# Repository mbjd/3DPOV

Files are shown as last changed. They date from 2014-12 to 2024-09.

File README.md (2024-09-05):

# 3DPOV

This is the github repo for my 3D persistence of vision display. Here you
can find the arduino/teensy source code (`./code/`), eagle schematic and
board files (`./Eagle/`), and the python program I wrote to simplify the
creation of images containing simple shapes (`./image_creation/`).

### Videos

[one](https://www.youtube.com/watch?v=bCETWNgBxbI) [two](https://www.youtube.com/watch?v=-gFsKhf5J-I)

### Summary

This was my Matura project (the end of (the equivalent of) high school in
Switzerland), and I did most of the work in the second half of 2014. You
can find various more detailed reports below, but here's a quick summary:

The *very* basic idea is this: We have a 2D display
and rotate it quickly through the third dimension. By controlling each 
pixel in a precisely timed way, we can light up a set of points in 3D 
space, but only at specific times (when the corresponding pixel is
physically at the right spot). When this rotation is fast enough, 
[persistence of vision](https://en.wikipedia.org/wiki/Persistence_of_vision) 
will make it seem like an actual 3D image is continuously displayed. 

The display itself consists of 10 LED rows mounted in a double-helix
arrangement. Each of them contains 16 RGB LEDs driven by three shift
registers, for a total of 480 LEDs or 160 Pixels.

The shift registers are controlled by a Teensy 3.1 microcontroller board
using an SPI bus (All 30 shift registers are daisy chained together). The
controller is mounted on a wooden disc below the ten LED boards.

All of this is mounted on a 4mm steel shaft, supplied with 3.3V DC using
two copper slip rings, and spun up to 60 Hz by a brushed DC motor. A hall
sensor and a magnet enable the controller to measure the rotational speed
and to adjust its timing, so that the image always stays still despite the
speed not being quite constant. The image is updated 100 times per
revolution, or 6000 times a second.

Currently there's no way to supply images at runtime, the display has to be
stopped so that a new program can be uploaded using the Teensy's USB port.

### Various versions of the paper

[Original in German](https://drive.google.com/file/d/0B2iq6C3wqe05aEx5dVFoNF9xR28/view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)

[English long version, not quite finished](https://github.com/mbjd/english-paper/blob/master/paper.pdf)

[English short version](https://github.com/mbjd/english-paper/blob/master/paper-short.pdf)

[Other english stuff](https://github.com/mbjd/english-paper)

### Press etc

[Hackaday article](http://hackaday.com/2016/11/16/spinning-3d-pov-display-as-a-high-school-term-project/)

[ETHZ D-ITET in German](https://www.ee.ethz.ch/de/news-und-veranstaltungen/d-itet-news-channel/2016/09/d-itet-student-gewinnt-forschungs-preis-.html) or [English](https://www.ee.ethz.ch/news-and-events/d-itet-news-channel/2016/09/d-itet-student-wins-research-award.html)

[Swiss Youth in Science article](http://web.archive.org/web/20161117130814/http://sjf.ch/eucys-2016-eth-student-gewinnt-forschungs-preis-am-ersten-studientag/)

[EUCYS 2016 link](http://eucys2016.eu/development-of-a-3d-display/)

### Links to discussion

[one](http://www.reddit.com/r/electronics/comments/2m6apx/finally_my_led_board_works_had_to_make_a_little/) [two](http://www.reddit.com/r/electronics/comments/2nrek4/almost_working_3d_pov_display/) [three](http://www.reddit.com/r/electronics/comments/2q9sg6/my_3d_pov_in_action_as_promised/)

### Photos

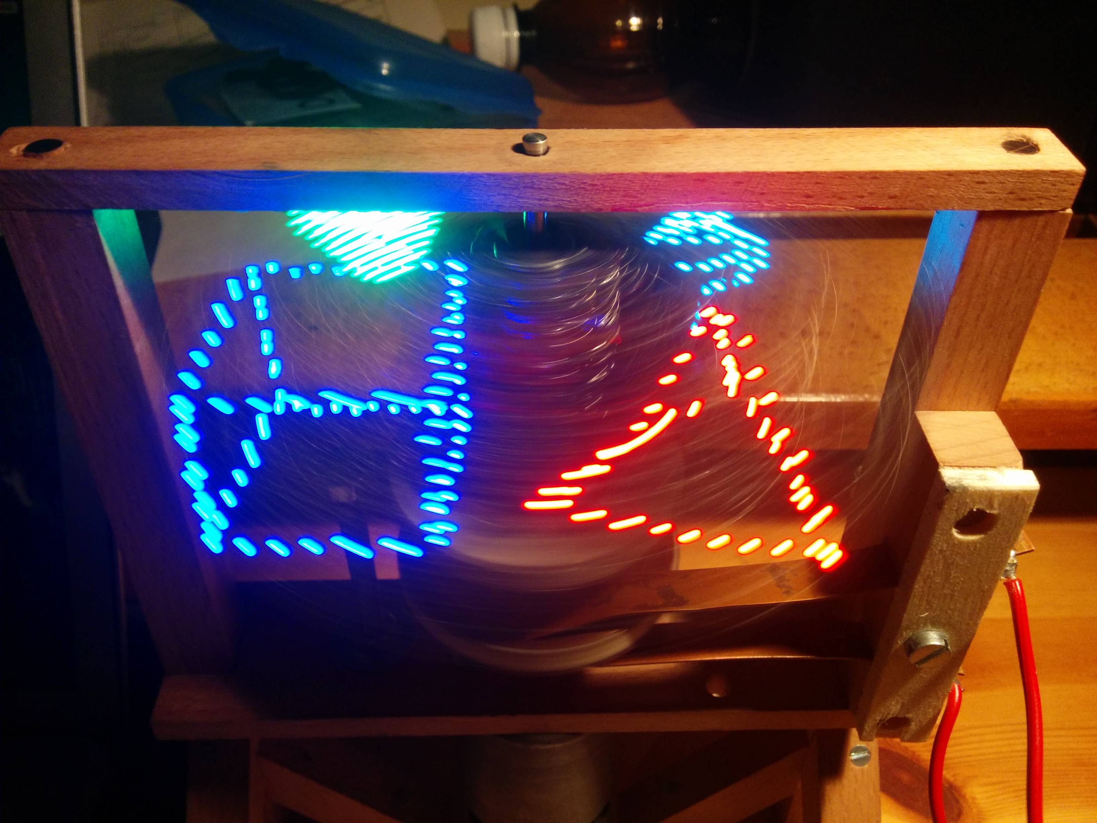
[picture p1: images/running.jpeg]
Photo of it in action


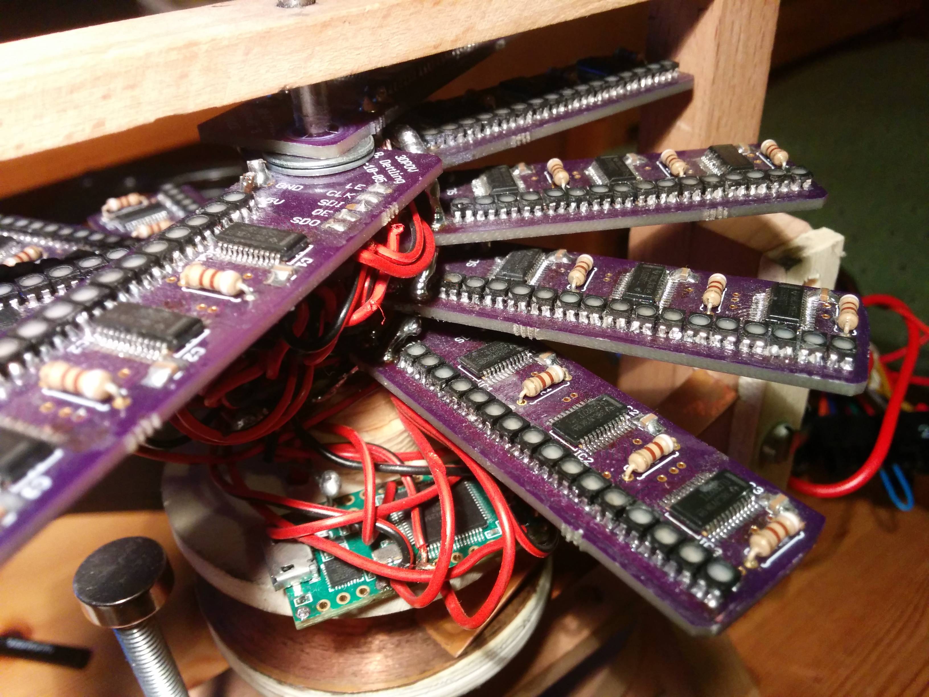
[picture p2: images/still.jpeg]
Photo of it standing still


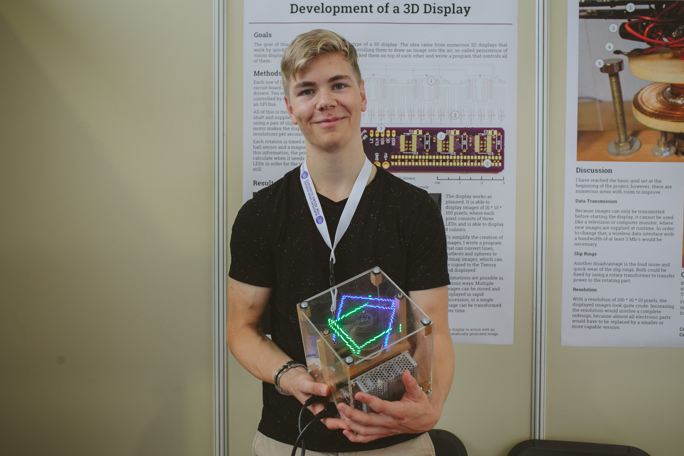
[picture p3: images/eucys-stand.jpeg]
Me at EUCYS 2016 being super happy


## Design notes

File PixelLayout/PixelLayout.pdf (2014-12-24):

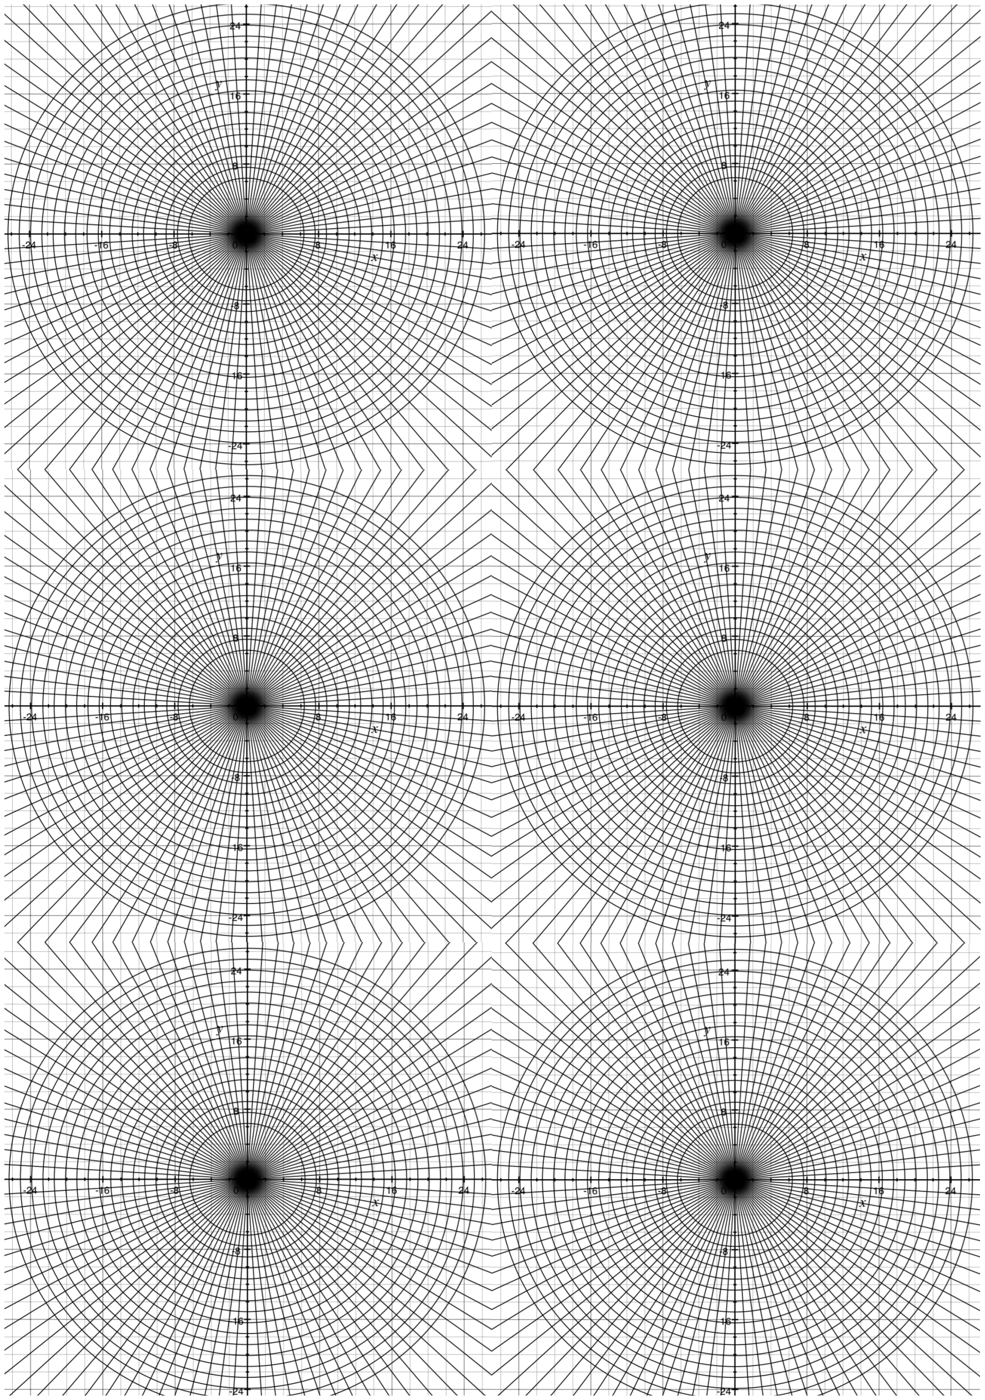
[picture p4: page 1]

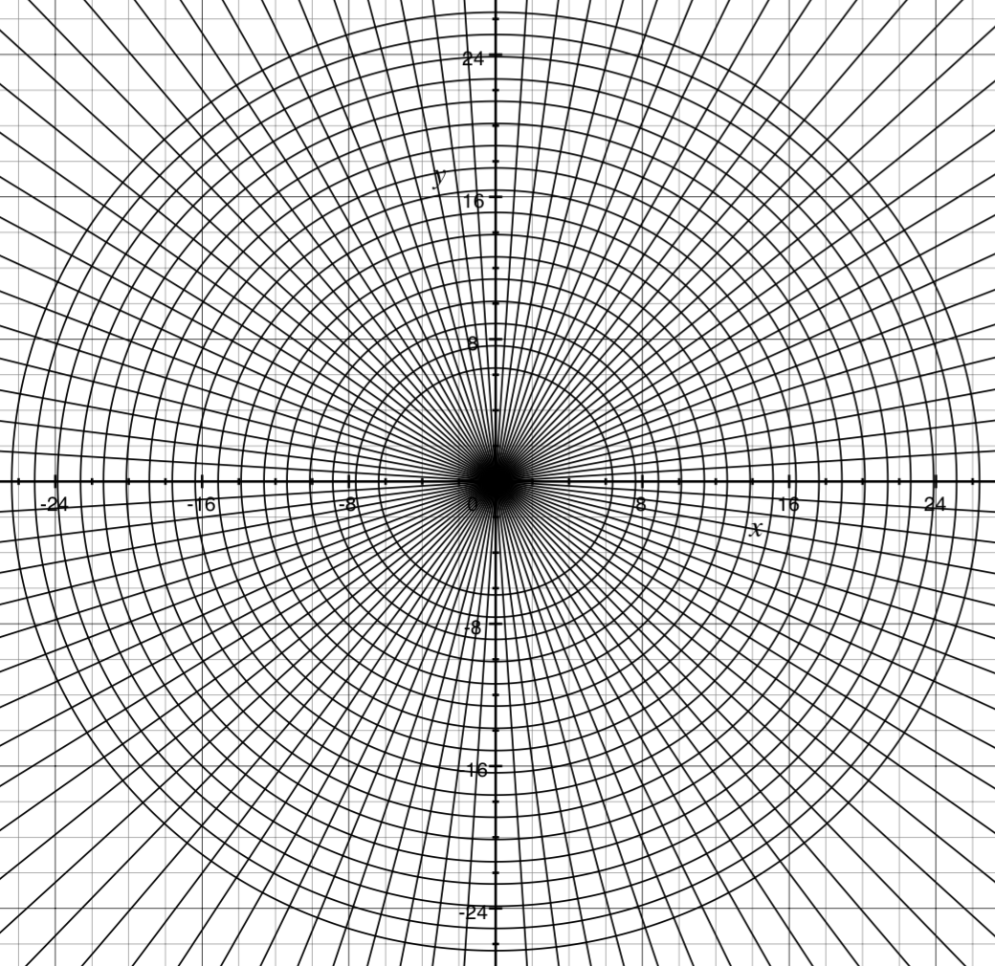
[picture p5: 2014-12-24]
PixelLayout/PixelLayout.png

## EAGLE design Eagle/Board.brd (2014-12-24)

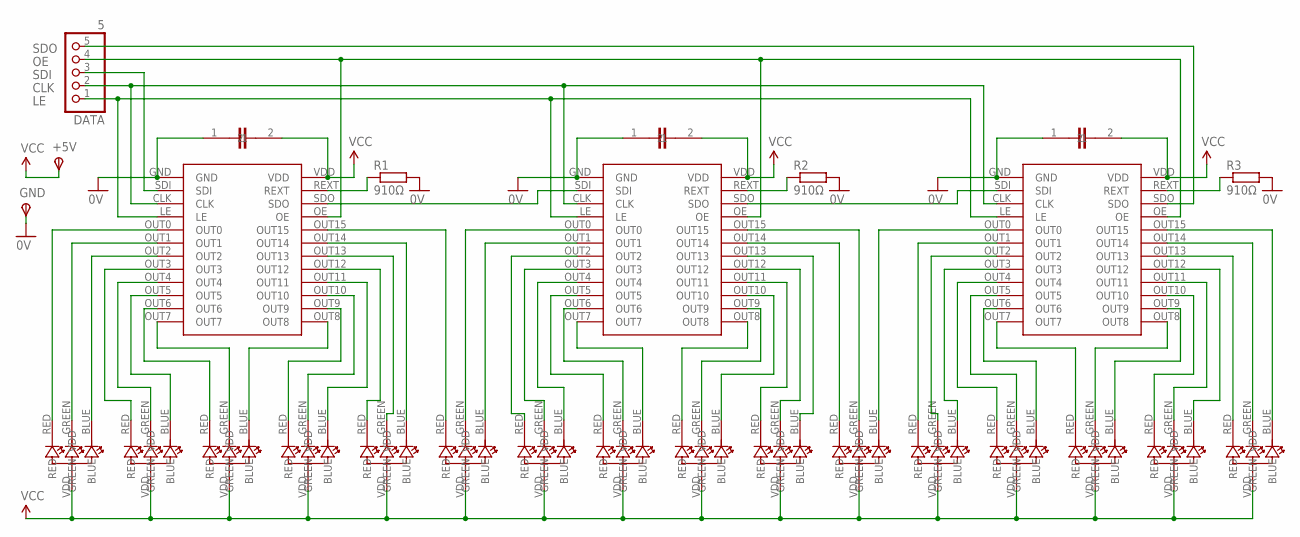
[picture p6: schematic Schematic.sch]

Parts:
+5V: TPSPAD1-20; P1-20
CAP1, CAP2, CAP3: 1µF; CAP
DATA: 5; 1X05
GND: TPSPAD1-20; P1-20
IC1, IC2, IC3: TLC5927; DBQ
R1, R2, R3: 910Ω; 0207/7
U$1, U$2, U$4, U$5, U$6, U$7, U$10, U$11, U$12, U$13, U$14, U$15, U$16, U$17, U$18, U$19: SMDLED

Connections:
0V: CAP1.1, CAP2.1, CAP3.1, GND.TP, IC1.GND, IC2.GND, IC3.GND, R1.2, R2.2, R3.2
CLK: DATA.2, IC1.CLK, IC2.CLK, IC3.CLK
LE: DATA.1, IC1.LE, IC2.LE, IC3.LE
unnamed: IC1.OUT0, U$4.RED
unnamed: IC1.OUT1, U$4.GREEN
unnamed: IC1.OUT2, U$4.BLUE
unnamed: IC1.OUT3, U$5.RED
unnamed: IC1.OUT4, U$5.GREEN
unnamed: IC1.OUT5, U$5.BLUE
unnamed: IC1.OUT7, U$6.GREEN
unnamed: IC1.OUT6, U$6.RED
unnamed: IC1.OUT8, U$6.BLUE
unnamed: IC1.OUT9, U$7.RED
unnamed: IC1.OUT10, U$7.GREEN
unnamed: IC1.OUT11, U$7.BLUE
unnamed: IC1.OUT12, U$2.RED
unnamed: IC1.OUT13, U$2.GREEN
unnamed: IC1.OUT14, U$2.BLUE
unnamed: IC1.OUT15, U$1.RED
unnamed: IC2.OUT0, U$1.GREEN
unnamed: IC2.OUT1, U$1.BLUE
unnamed: IC2.OUT2, U$10.RED
unnamed: IC2.OUT3, U$10.GREEN
unnamed: IC2.OUT4, U$10.BLUE
unnamed: IC2.OUT7, U$11.BLUE
unnamed: IC2.OUT6, U$11.GREEN
unnamed: IC2.OUT5, U$11.RED
unnamed: IC2.OUT11, U$13.RED
unnamed: IC2.OUT12, U$13.GREEN
unnamed: IC2.OUT13, U$13.BLUE
unnamed: IC2.OUT14, U$14.RED
unnamed: IC2.OUT15, U$14.GREEN
unnamed: IC3.OUT0, U$14.BLUE
unnamed: IC3.OUT1, U$15.RED
unnamed: IC3.OUT2, U$15.GREEN
unnamed: IC3.OUT3, U$15.BLUE
unnamed: IC3.OUT4, U$16.RED
unnamed: IC3.OUT5, U$16.GREEN
unnamed: IC3.OUT7, U$17.RED
unnamed: IC3.OUT6, U$16.BLUE
unnamed: IC3.OUT8, U$17.GREEN
unnamed: IC3.OUT9, U$17.BLUE
unnamed: IC3.OUT10, U$18.RED
unnamed: IC3.OUT11, U$18.GREEN
unnamed: IC3.OUT12, U$18.BLUE
unnamed: IC3.OUT13, U$19.RED
unnamed: IC3.OUT14, U$19.GREEN
unnamed: IC3.OUT15, U$19.BLUE
unnamed: IC3.REXT, R3.1
unnamed: IC1.SDO, IC2.SDI
unnamed: IC2.SDO, IC3.SDI
unnamed: IC2.REXT, R2.1
unnamed: IC1.REXT, R1.1
unnamed: IC2.OUT8, U$12.RED
unnamed: IC2.OUT9, U$12.GREEN
unnamed: IC2.OUT10, U$12.BLUE
OE: DATA.4, IC1.OE, IC2.OE, IC3.OE
SDI: DATA.3, IC1.SDI
SDO: DATA.5, IC3.SDO
VCC: +5V.TP, CAP1.2, CAP2.2, CAP3.2, IC1.VDD, IC2.VDD, IC3.VDD, U$1.VDD, U$2.VDD, U$4.VDD, U$5.VDD, U$6.VDD, U$7.VDD, U$10.VDD, U$11.VDD, U$12.VDD, U$13.VDD, U$14.VDD, U$15.VDD, U$16.VDD, U$17.VDD, U$18.VDD, U$19.VDD

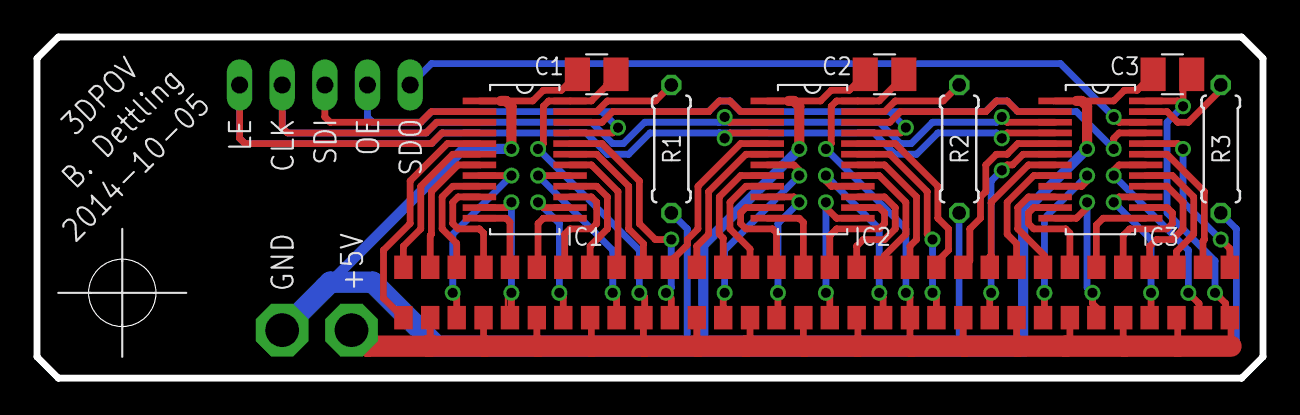
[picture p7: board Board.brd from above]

Board: 2 copper layers, 73.0 x 20.3 mm, 28 parts (0 on the bottom side), 60 nets.

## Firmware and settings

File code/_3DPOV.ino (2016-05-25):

#include <SPI.h>

const byte image[100][10][16] = {
	// 00
	{
		{0b00000000, 0b00000000, 0b00000000, 0b00000000, 0b00000000, 0b00000000},
		{0b00000000, 0b00000000, 0b00000000, 0b00000000, 0b00000000, 0b00000000},
		{0b00000000, 0b00000000, 0b00000000, 0b00000000, 0b00000000, 0b00000000},
		{0b00000000, 0b00000000, 0b00000000, 0b00000000, 0b00000000, 0b00000000},
		{0b00000000, 0b00000000, 0b00000000, 0b00000000, 0b00000000, 0b00000000},
		{0b00000000, 0b00000000, 0b00000000, 0b00000000, 0b00000000, 0b00000000},
		{0b00000000, 0b00000000, 0b00000000, 0b00000000, 0b00000000, 0b00000000},
		{0b00000000, 0b00000000, 0b00000000, 0b00000000, 0b00000000, 0b00000000},
		{0b00000000, 0b00000000, 0b00000000, 0b00000000, 0b00000000, 0b00000000},
		{0b00000000, 0b00000000, 0b00000000, 0b00000000, 0b00000000, 0b00000000}
	},

	// 01
	{
		{0b00000000, 0b00000000, 0b00000000, 0b00000000, 0b00000000, 0b00000000},
		{0b00000000, 0b00000000, 0b00000000, 0b00000000, 0b00000000, 0b00000000},
		{0b00000000, 0b00000000, 0b00000000, 0b00000000, 0b00000000, 0b00000000},
		{0b00000000, 0b00000000, 0b00000000, 0b00000000, 0b00000000, 0b00000000},
		{0b00000000, 0b00000000, 0b00000000, 0b00000000, 0b00000000, 0b00000000},
		{0b00000000, 0b00000000, 0b00000000, 0b00000000, 0b00000000, 0b00000000},
		{0b00000000, 0b00000000, 0b00000000, 0b00000000, 0b00000000, 0b00000000},
		{0b00000000, 0b00000000, 0b00000000, 0b00000000, 0b00000000, 0b00000000},
		{0b00000000, 0b00000000, 0b00000000, 0b00000000, 0b00000000, 0b00000000},
		{0b00000000, 0b00000000, 0b00000000, 0b00000000, 0b00000000, 0b00000000}
	},

	// 02
	{
		{0b00000000, 0b00000000, 0b00000000, 0b00000000, 0b00000000, 0b00000000},
		{0b00000000, 0b00000000, 0b00000000, 0b00000000, 0b00000000, 0b00000000},
		{0b00000000, 0b00000000, 0b00000000, 0b00000000, 0b00000000, 0b00000000},
		{0b00000000, 0b00000000, 0b00000000, 0b00000000, 0b00000000, 0b00000000},
		{0b00000000, 0b00000000, 0b00000000, 0b00000000, 0b00000000, 0b00000000},
		{0b00000000, 0b00000000, 0b00000000, 0b00000000, 0b00000000, 0b00000000},
		{0b00000000, 0b00000000, 0b00000000, 0b00000000, 0b00000000, 0b00000000},
		{0b00000000, 0b00000000, 0b00000000, 0b00000000, 0b00000000, 0b00000000},
		{0b00000000, 0b00000000, 0b00000000, 0b00000000, 0b00000000, 0b00000000},
		{0b00000000, 0b00000000, 0b00000000, 0b00000000, 0b00000000, 0b00000000}
	},

	// 03
	{
		{0b00000000, 0b00000000, 0b00000000, 0b00000000, 0b00000000, 0b00000000},
		{0b00000000, 0b00000000, 0b00000000, 0b00000000, 0b00000000, 0b00000000},
		{0b00000000, 0b00000000, 0b00000000, 0b00000000, 0b00000000, 0b00000000},
		{0b00000000, 0b00000000, 0b00000000, 0b00000000, 0b00000000, 0b00000000},
		{0b00000000, 0b00000000, 0b00000000, 0b00000000, 0b00000000, 0b00000000},
		{0b00000000, 0b00000000, 0b00000000, 0b00000000, 0b00000000, 0b00000000},
		{0b00000000, 0b00000000, 0b00000000, 0b00000000, 0b00000000, 0b00000000},
		{0b00000000, 0b00000000, 0b00000000, 0b00000000, 0b00000000, 0b00000000},
		{0b00000000, 0b00000000, 0b00000000, 0b00000000, 0b00000000, 0b00000000},
		{0b00000000, 0b00000000, 0b00000000, 0b00000000, 0b00000000, 0b00000000}
	},

	// 04
	{
		{0b00000000, 0b00000000, 0b00000000, 0b00000000, 0b00000000, 0b00000000},
		{0b00000000, 0b00000000, 0b00000000, 0b00000000, 0b00000000, 0b00000000},
		{0b00000000, 0b00000000, 0b00000000, 0b00000000, 0b00000000, 0b00000000},
		{0b00000000, 0b00000000, 0b00000000, 0b00000000, 0b00000000, 0b00000000},
		{0b00000000, 0b00000000, 0b00000000, 0b00000000, 0b00000000, 0b00000000},
		{0b00000000, 0b00000000, 0b00000000, 0b00000000, 0b00000000, 0b00000000},
		{0b00000000, 0b00000000, 0b00000000, 0b00000000, 0b00000000, 0b00000000},
		{0b00000000, 0b00000000, 0b00000000, 0b00000000, 0b00000000, 0b00000000},
		{0b00000000, 0b00000000, 0b00000000, 0b00000000, 0b00000000, 0b00000000},
		{0b00000000, 0b00000000, 0b00000000, 0b00000000, 0b00000000, 0b00000000}
	},

	// 05
	{
		{0b00000000, 0b00000000, 0b00000000, 0b00000000, 0b00000000, 0b00000000},
		{0b00000000, 0b00000000, 0b00000000, 0b00000000, 0b00000000, 0b00000000},
		{0b00000000, 0b00000000, 0b00000000, 0b00000000, 0b00000000, 0b00000000},
		{0b00000000, 0b00000000, 0b00000000, 0b00000000, 0b00000000, 0b00000000},
		{0b00000000, 0b00000000, 0b00000000, 0b00000000, 0b00000000, 0b00000000},
		{0b00000000, 0b00000000, 0b00000000, 0b00000000, 0b00000000, 0b00000000},
		{0b00000000, 0b00000000, 0b00000000, 0b00000000, 0b00000000, 0b00000000},
		{0b00000000, 0b00000000, 0b00000000, 0b00000000, 0b00000000, 0b00000000},
		{0b00000000, 0b00000000, 0b00000000, 0b00000000, 0b00000000, 0b00000000},
		{0b00000000, 0b00000000, 0b00000000, 0b00000000, 0b00000000, 0b00000000}
	},

	// 06
	{
		{0b00000000, 0b00000000, 0b00000000, 0b00000000, 0b00000000, 0b00000000},
		{0b00000000, 0b00000000, 0b00000000, 0b00000000, 0b00000000, 0b00000000},
		{0b00000000, 0b00000000, 0b00000000, 0b00000000, 0b00000000, 0b00000000},
		{0b00000000, 0b00000000, 0b00000000, 0b00000000, 0b00000000, 0b00000000},
		{0b00000000, 0b00000000, 0b00000000, 0b00000000, 0b00000000, 0b00000000},
		{0b00000000, 0b00000000, 0b00000000, 0b00000000, 0b00000000, 0b00000000},
		{0b00000000, 0b00000000, 0b00000000, 0b00000000, 0b00000000, 0b00000000},
		{0b00000000, 0b00000000, 0b00000000, 0b00000000, 0b00000000, 0b00000000},
		{0b00000000, 0b00000000, 0b00000000, 0b00000000, 0b00000000, 0b00000000},
		{0b00000000, 0b00000000, 0b00000000, 0b00000000, 0b00000000, 0b00000000}
	},

	// 07
	{
		{0b00000000, 0b00000000, 0b00000000, 0b00000000, 0b00000000, 0b00000000},
		{0b00000000, 0b00000000, 0b00000000, 0b00000000, 0b00000000, 0b00000000},
		{0b00000000, 0b00000000, 0b00000000, 0b00000000, 0b00000000, 0b00000000},
		{0b00000000, 0b00000000, 0b00000000, 0b00000000, 0b00000000, 0b00000000},
		{0b00000000, 0b00000000, 0b00000000, 0b00000000, 0b00000000, 0b00000000},
		{0b00000000, 0b00000000, 0b00000000, 0b00000000, 0b00000000, 0b00000000},
		{0b00000000, 0b00000000, 0b00000000, 0b00000000, 0b00000000, 0b00000000},
		{0b00000000, 0b00000000, 0b00000000, 0b00000000, 0b00000000, 0b00000000},
		{0b00000000, 0b00000000, 0b00000000, 0b00000000, 0b00000000, 0b00000000},
		{0b00000000, 0b00000000, 0b00000000, 0b00000000, 0b00000000, 0b00000000}
	},

	// 08
	{
		{0b00000000, 0b00000000, 0b00000000, 0b00000000, 0b00000000, 0b00000000},
		{0b00000000, 0b00000000, 0b00000000, 0b00000000, 0b00000000, 0b00000000},
		{0b00000000, 0b00000000, 0b00000000, 0b00000000, 0b00000000, 0b00000000},
		{0b00000000, 0b00000000, 0b00000000, 0b00000000, 0b00000000, 0b00000000},
		{0b00000000, 0b00000000, 0b00000000, 0b00000000, 0b00000000, 0b00000000},
		{0b00000000, 0b00000000, 0b00000000, 0b00000000, 0b00000000, 0b00000000},
		{0b00000000, 0b00000000, 0b00000000, 0b00000000, 0b00000000, 0b00000000},
		{0b00000000, 0b00000000, 0b00000000, 0b00000000, 0b00000000, 0b00000000},
		{0b00000000, 0b00000000, 0b00000000, 0b00000000, 0b00000000, 0b00000000},
		{0b00000000, 0b00000000, 0b00000000, 0b00000000, 0b00000000, 0b00000000}
	},

	// 09
	{
		{0b00000000, 0b00000000, 0b00000000, 0b00000000, 0b00000000, 0b00000000},
		{0b00000000, 0b00000000, 0b00000000, 0b00000000, 0b00000000, 0b00000000},
		{0b00000000, 0b00000000, 0b00000000, 0b00000000, 0b00000000, 0b00000000},
		{0b00000000, 0b00000000, 0b00000000, 0b00000000, 0b00000000, 0b00000000},
		{0b00000000, 0b00000000, 0b00000000, 0b00000000, 0b00000000, 0b00000000},
		{0b00000000, 0b00000000, 0b00000000, 0b00000000, 0b00000000, 0b00000000},
		{0b00000000, 0b00000000, 0b00000000, 0b00000000, 0b00000000, 0b00000000},
		{0b00000000, 0b00000000, 0b00000000, 0b00000000, 0b00000000, 0b00000000},
		{0b00000000, 0b00000000, 0b00000000, 0b00000000, 0b00000000, 0b00000000},
		{0b00000000, 0b00000000, 0b00000000, 0b00000000, 0b00000000, 0b00000000}
	},

	// 10
	{
		{0b00000000, 0b00000000, 0b00000000, 0b00000000, 0b00000000, 0b00000000},
		{0b00000000, 0b00000000, 0b00000000, 0b00000000, 0b00000000, 0b00000000},
		{0b00000000, 0b00000000, 0b00000000, 0b00000000, 0b00000000, 0b00000000},
		{0b00000000, 0b00000000, 0b00000000, 0b00000000, 0b00000000, 0b00000000},
		{0b00000000, 0b00000000, 0b00000000, 0b00000000, 0b00000000, 0b00000000},
		{0b00000000, 0b00000000, 0b00000000, 0b00000000, 0b00000000, 0b00000000},
		{0b00000000, 0b00000000, 0b00000000, 0b00000000, 0b00000000, 0b00000000},
		{0b00000000, 0b00000000, 0b00000000, 0b00000000, 0b00000000, 0b00000000},
		{0b00000000, 0b00000000, 0b00000000, 0b00000000, 0b00000000, 0b00000000},
		{0b00000000, 0b00000000, 0b00000000, 0b00000000, 0b00000000, 0b00000000}
	},

	// 11
	{
		{0b00000000, 0b00000000, 0b00000000, 0b00000000, 0b00000000, 0b00000000},
		{0b00000000, 0b00000000, 0b00000000, 0b00000000, 0b00000000, 0b00000000},
		{0b00000000, 0b00000000, 0b00000000, 0b00000000, 0b00000000, 0b00000000},
		{0b00000000, 0b00000000, 0b00000000, 0b00000000, 0b00000000, 0b00000000},
		{0b00000000, 0b00000000, 0b00000000, 0b00000000, 0b00000000, 0b00000000},
		{0b00000000, 0b00000000, 0b00000000, 0b00000000, 0b00000000, 0b00000000},
		{0b00000000, 0b00000000, 0b00000000, 0b00000000, 0b00000000, 0b00000000},
		{0b00000000, 0b00000000, 0b00000000, 0b00000000, 0b00000000, 0b00000000},
		{0b00000000, 0b00000000, 0b00000000, 0b00000000, 0b00000000, 0b00000000},
		{0b00000000, 0b00000000, 0b00000000, 0b00000000, 0b00000000, 0b00000000}
	},

	// 12
	{
		{0b00000000, 0b00000000, 0b00000000, 0b00000000, 0b00000000, 0b00000000},
		{0b00000000, 0b00000000, 0b00000000, 0b00000000, 0b00000000, 0b00000000},
		{0b00000000, 0b00000000, 0b00000000, 0b00000000, 0b00000000, 0b00000000},
		{0b00000000, 0b00000000, 0b00000000, 0b00000000, 0b00000000, 0b00000000},
		{0b00000000, 0b00000000, 0b00000000, 0b00000000, 0b00000000, 0b00000000},
		{0b00000000, 0b00000000, 0b00000000, 0b00000000, 0b00000000, 0b00000000},
		{0b00000000, 0b00000000, 0b00000000, 0b00000000, 0b00000000, 0b00000000},
		{0b00000000, 0b00000000, 0b00000000, 0b00000000, 0b00000000, 0b00000000},
		{0b00000000, 0b00000000, 0b00000000, 0b00000000, 0b00000000, 0b00000000},
		{0b00000000, 0b00000000, 0b00000000, 0b00000000, 0b00000000, 0b00000000}
	},

	// 13
	{
		{0b00000000, 0b00000000, 0b00000000, 0b00000000, 0b00000000, 0b00000000},
		{0b00000000, 0b00000000, 0b00000000, 0b00000000, 0b00000000, 0b00000000},
		{0b00000000, 0b00000000, 0b00000000, 0b00000000, 0b00000000, 0b00000000},
		{0b00000000, 0b00000000, 0b00000000, 0b00000000, 0b00000000, 0b00000000},
		{0b00000000, 0b00000000, 0b00000000, 0b00000000, 0b00000000, 0b00000000},
		{0b00000000, 0b00000000, 0b00000000, 0b00000000, 0b00000000, 0b00000000},
		{0b00000000, 0b00000000, 0b00000000, 0b00000000, 0b00000000, 0b00000000},
		{0b00000000, 0b00000000, 0b00000000, 0b00000000, 0b00000000, 0b00000000},
		{0b00000000, 0b00000000, 0b00000000, 0b00000000, 0b00000000, 0b00000000},
		{0b00000000, 0b00000000, 0b00000000, 0b00000000, 0b00000000, 0b00000000}
	},

	// 14
	{
		{0b00000000, 0b00000000, 0b00000000, 0b00000000, 0b00000000, 0b00000000},
		{0b00000000, 0b00000000, 0b00000000, 0b00000000, 0b00000000, 0b00000000},
		{0b00000000, 0b00000000, 0b00000000, 0b00000000, 0b00000000, 0b00000000},
		{0b00000000, 0b00000000, 0b00000000, 0b00000000, 0b00000000, 0b00000000},
		{0b00000000, 0b00000000, 0b00000000, 0b00000000, 0b00000000, 0b00000000},
		{0b00000000, 0b00000000, 0b00000000, 0b00000000, 0b00000000, 0b00000000},
		{0b00000000, 0b00000000, 0b00000000, 0b00000000, 0b00000000, 0b00000000},
		{0b00000000, 0b00000000, 0b00000000, 0b00000000, 0b00000000, 0b00000000},
		{0b00000000, 0b00000000, 0b00000000, 0b00000000, 0b00000000, 0b00000000},
		{0b00000000, 0b00000000, 0b00000000, 0b00000000, 0b00000000, 0b00000000}
	},

	// 15
	{
		{0b00000000, 0b00000000, 0b00000000, 0b00000000, 0b00000000, 0b00000000},
		{0b00000000, 0b00000000, 0b00000000, 0b00000000, 0b00000000, 0b00000000},
		{0b00000000, 0b00000000, 0b00000000, 0b00000000, 0b00000000, 0b00000000},
		{0b00000000, 0b00000000, 0b00000000, 0b00000000, 0b00000000, 0b00000000},
		{0b00000000, 0b00000000, 0b00000000, 0b00000000, 0b00000000, 0b00000000},
		{0b00000000, 0b00000000, 0b00000000, 0b00000000, 0b00000000, 0b00000000},
		{0b00000000, 0b00000000, 0b00000000, 0b00000000, 0b00000000, 0b00000000},
		{0b00000000, 0b00000000, 0b00000000, 0b00000000, 0b00000000, 0b00000000},
		{0b00000000, 0b00000000, 0b00000000, 0b00000000, 0b00000000, 0b00000000},
		{0b00000000, 0b00000000, 0b00000000, 0b00000000, 0b00000000, 0b00000000}
	},

	// 16
	{
		{0b00000000, 0b00000000, 0b00000000, 0b00000000, 0b00000000, 0b00000000},
		{0b00000000, 0b00000000, 0b00000000, 0b00000000, 0b00000000, 0b00000000},
		{0b00000000, 0b00000000, 0b00000000, 0b00000000, 0b00000000, 0b00000000},
		{0b00000000, 0b00000000, 0b00000000, 0b00000000, 0b00000000, 0b00000000},
		{0b00000000, 0b00000000, 0b00000000, 0b00000000, 0b00000000, 0b00000000},
		{0b00000000, 0b00000000, 0b00000000, 0b00000000, 0b00000000, 0b00000000},
		{0b00000000, 0b00000000, 0b00000000, 0b00000000, 0b00000000, 0b00000000},
		{0b00000000, 0b00000000, 0b00000000, 0b00000000, 0b00000000, 0b00000000},
		{0b00000000, 0b00000000, 0b00000000, 0b00000000, 0b00000000, 0b00000000},
		{0b00000000, 0b00000000, 0b00000000, 0b00000000, 0b00000000, 0b00000000}
	},

	// 17
	{
		{0b00000000, 0b00000000, 0b00000000, 0b00000000, 0b00000000, 0b00000000},
		{0b00000000, 0b00000000, 0b00000000, 0b00000000, 0b00000000, 0b00000000},
		{0b00000000, 0b00000000, 0b00000000, 0b00000000, 0b00000000, 0b00000000},
		{0b00000000, 0b00000000, 0b00000000, 0b00000000, 0b00000000, 0b00000000},
		{0b00000000, 0b00000000, 0b00000000, 0b00000000, 0b00000000, 0b00000000},
		{0b00000000, 0b00000000, 0b00000000, 0b00000000, 0b00000000, 0b00000000},
		{0b00000000, 0b00000000, 0b00000000, 0b00000000, 0b00000000, 0b00000000},
		{0b00000000, 0b00000000, 0b00000000, 0b00000000, 0b00000000, 0b00000000},
		{0b00000000, 0b00000000, 0b00000000, 0b00000000, 0b00000000, 0b00000000},
		{0b00000000, 0b00000000, 0b00000000, 0b00000000, 0b00000000, 0b00000000}
	},

	// 18
	{
		{0b00000000, 0b00000000, 0b00000000, 0b00000000, 0b00000000, 0b00000000},
		{0b00000000, 0b00000000, 0b00000000, 0b00000000, 0b00000000, 0b00000000},
		{0b00000000, 0b00000000, 0b00000000, 0b00000000, 0b00000000, 0b00000000},
		{0b00000000, 0b00000000, 0b00000000, 0b00000000, 0b00000000, 0b00000000},
		{0b00000000, 0b00000000, 0b00000000, 0b00000000, 0b00000000, 0b00000000},
		{0b00000000, 0b00000000, 0b00000000, 0b00000000, 0b00000000, 0b00000000},
		{0b00000000, 0b00000000, 0b00000000, 0b00000000, 0b00000000, 0b00000000},
		{0b00000000, 0b00000000, 0b00000000, 0b00000000, 0b00000000, 0b00000000},
		{0b00000000, 0b00000000, 0b00000000, 0b00000000, 0b00000000, 0b00000000},
		{0b00000000, 0b00000000, 0b00000000, 0b00000000, 0b00000000, 0b00000000}
	},

	// 19
	{
		{0b00000000, 0b00000000, 0b00000000, 0b00000000, 0b00000000, 0b00000000},
		{0b00000000, 0b00000000, 0b00000000, 0b00000000, 0b00000000, 0b00000000},
		{0b00000000, 0b00000000, 0b00000000, 0b00000000, 0b00000000, 0b00000000},
		{0b00000000, 0b00000000, 0b00000000, 0b00000000, 0b00000000, 0b00000000},
		{0b00000000, 0b00000000, 0b00000000, 0b00000000, 0b00000000, 0b00000000},
		{0b00000000, 0b00000000, 0b00000000, 0b00000000, 0b00000000, 0b00000000},
		{0b00000000, 0b00000000, 0b00000000, 0b00000000, 0b00000000, 0b00000000},
		{0b00000000, 0b00000000, 0b00000000, 0b00000000, 0b00000000, 0b00000000},
		{0b00000000, 0b00000000, 0b00000000, 0b00000000, 0b00000000, 0b00000000},
		{0b00000000, 0b00000000, 0b00000000, 0b00000000, 0b00000000, 0b00000000}
	},

	// 20
	{
		{0b00000000, 0b00000000, 0b00000000, 0b00000000, 0b00000000, 0b00000000},
		{0b00000000, 0b00000000, 0b00000000, 0b00000000, 0b00000000, 0b00000000},
		{0b00000000, 0b00000000, 0b00000000, 0b00000000, 0b00000000, 0b00000000},
		{0b00000000, 0b00000000, 0b00000000, 0b00000000, 0b00000000, 0b00000000},
		{0b00000000, 0b00000000, 0b00000000, 0b00000000, 0b00000000, 0b00000000},
		{0b00000000, 0b00000000, 0b00000000, 0b00000000, 0b00000000, 0b00000000},
		{0b00000000, 0b00000000, 0b00000000, 0b00000000, 0b00000000, 0b00000000},
		{0b00000000, 0b00000000, 0b00000000, 0b00000000, 0b00000000, 0b00000000},
		{0b00000000, 0b00000000, 0b00000000, 0b00000000, 0b00000000, 0b00000000},
		{0b00000000, 0b00000000, 0b00000000, 0b00000000, 0b00000000, 0b00000000}
	},

	// 21
	{
		{0b00000000, 0b00000000, 0b00000000, 0b00000000, 0b00000000, 0b00000000},
		{0b00000000, 0b00000000, 0b00000000, 0b00000000, 0b00000000, 0b00000000},
		{0b00000000, 0b00000000, 0b00000000, 0b00000000, 0b00000000, 0b00000000},
		{0b00000000, 0b00000000, 0b00000000, 0b00000000, 0b00000000, 0b00000000},
		{0b00000000, 0b00000000, 0b00000000, 0b00000000, 0b00000000, 0b00000000},
		{0b00000000, 0b00000000, 0b00000000, 0b00000000, 0b00000000, 0b00000000},
		{0b00000000, 0b00000000, 0b00000000, 0b00000000, 0b00000000, 0b00000000},
		{0b00000000, 0b00000000, 0b00000000, 0b00000000, 0b00000000, 0b00000000},
		{0b00000000, 0b00000000, 0b00000000, 0b00000000, 0b00000000, 0b00000000},
		{0b00000000, 0b00000000, 0b00000000, 0b00000000, 0b00000000, 0b00000000}
	},

	// 22
	{
		{0b00000000, 0b00000000, 0b00000000, 0b00000000, 0b00000000, 0b00000000},
		{0b00000000, 0b00000000, 0b00000000, 0b00000000, 0b00000000, 0b00000000},
		{0b00000000, 0b00000000, 0b00000000, 0b00000000, 0b00000000, 0b00000000},
		{0b00000000, 0b00000000, 0b00000000, 0b00000000, 0b00000000, 0b00000000},
		{0b00000000, 0b00000000, 0b00000000, 0b00000000, 0b00000000, 0b00000000},
		{0b00000000, 0b00000000, 0b00000000, 0b00000000, 0b00000000, 0b00000000},
		{0b00000000, 0b00000000, 0b00000000, 0b00000000, 0b00000000, 0b00000000},
		{0b00000000, 0b00000000, 0b00000000, 0b00000000, 0b00000000, 0b00000000},
		{0b00000000, 0b00000000, 0b00000000, 0b00000000, 0b00000000, 0b00000000},
		{0b00000000, 0b00000000, 0b00000000, 0b00000000, 0b00000000, 0b00000000}
	},

	// 23
	{
		{0b00000000, 0b00000000, 0b00000000, 0b00000000, 0b00000000, 0b00000000},
		{0b00000000, 0b00000000, 0b00000000, 0b00000000, 0b00000000, 0b00000000},
		{0b00000000, 0b00000000, 0b00000000, 0b00000000, 0b00000000, 0b00000000},
		{0b00000000, 0b00000000, 0b00000000, 0b00000000, 0b00000000, 0b00000000},
		{0b00000000, 0b00000000, 0b00000000, 0b00000000, 0b00000000, 0b00000000},
		{0b00000000, 0b00000000, 0b00000000, 0b00000000, 0b00000000, 0b00000000},
		{0b00000000, 0b00000000, 0b00000000, 0b00000000, 0b00000000, 0b00000000},
		{0b00000000, 0b00000000, 0b00000000, 0b00000000, 0b00000000, 0b00000000},
		{0b00000000, 0b00000000, 0b00000000, 0b00000000, 0b00000000, 0b00000000},
		{0b00000000, 0b00000000, 0b00000000, 0b00000000, 0b00000000, 0b00000000}
	},

	// 24
	{
		{0b00000000, 0b00000000, 0b00000000, 0b00000000, 0b00000000, 0b00000000},
		{0b00000000, 0b00000000, 0b00000000, 0b00000000, 0b00000000, 0b00000000},
		{0b00000000, 0b00000000, 0b00000000, 0b00000000, 0b00000000, 0b00000000},
		{0b00000000, 0b00000000, 0b00000000, 0b00000000, 0b00000000, 0b00000000},
		{0b00000000, 0b00000000, 0b00000000, 0b00000000, 0b00000000, 0b00000000},
		{0b00000000, 0b00000000, 0b00000000, 0b00000000, 0b00000000, 0b00000000},
		{0b00000000, 0b00000000, 0b00000000, 0b00000000, 0b00000000, 0b00000000},
		{0b00000000, 0b00000000, 0b00000000, 0b00000000, 0b00000000, 0b00000000},
		{0b00000000, 0b00000000, 0b00000000, 0b00000000, 0b00000000, 0b00000000},
		{0b00000000, 0b00000000, 0b00000000, 0b00000000, 0b00000000, 0b00000000}
	},
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
void loop(void)
{
	// Continuously check if we should refresh the LED data
	if (running && (microsSinceMagnet > nextPixelMicros))
	{
		sendData();
	}
}

void timerUpdate(void)
{
	// Set a flag that is read at the end of sendData so it knows if it's
	// been interrupted
	interrupted = true;
	running = true;

	// Calculate the new pixel duration
	microsPerPixel = ((float) microsSinceMagnet) / 100.0;

	// Reset timer & wait half a period before the first LED refresh 
	microsSinceMagnet = 0;
	nextPixelMicros = 0;

	// Always 0 if !rotating, sawtooth from 0 to 99 otherwise
	currentPixel = startPixel;

	// Let the image "fall down"
	if (waterfall && evenRotation)
	{
		// Sawtooth from 9 to 0
		if (boardOffset == 0)
		{
			boardOffset = 10;
		}

		boardOffset--;
	}

	evenRotation = !evenRotation;

	// Let the image rotate counterclockwise
	if (rotating)
	{
		// Sawtooth from 0 to 99
		startPixel++;
		startPixel %= 100;
	}
}

void sendData(void)
{
	// Reset the interrupted flag
	interrupted = false;

	SPI.beginTransaction(mySettings);

	// Send the data, taking into account the vertical board offset in
	// case waterfall is enabled. Return if there's been an interrupt
	// to not send any unnecessary data.
	for (int i = 0; i < 5; i++)
	{
		if (interrupted) return;

		currentBoard = 2*i;
		offsetBoard = (currentBoard + boardOffset) % 10;
		offsetPixel = (currentPixel + 8*i + 70) % 100;

		for (int j = 5; j >= 0; j--)
		{
			SPI.transfer(image[offsetPixel][offsetBoard][j]);
		}

		if (interrupted) return;

		currentBoard++;
		offsetBoard = (currentBoard + boardOffset) % 10;
		offsetPixel = (offsetPixel + 50) % 100;

		for (int j = 5; j >= 0; j--)
		{
			SPI.transfer(image[offsetPixel][offsetBoard][j]);
		}
	}

	SPI.endTransaction();
	pulseLatch();

	// Only modify the global timing variables if no interrupt has been fired
	// while this function was running. Otherwise we're executing code from the
	// old revolution when the new one has already started, and the image becomes
	// jittery.
	if (!interrupted)
	{
		currentPixel++;
		nextPixelMicros += microsPerPixel;
	}
}

// Short pulse on the latch pin in order to send the data from the LED driver's
// data transmission registers to the output registers
inline void pulseLatch(void)
{
	digitalWrite(latchPin, HIGH);
	delayMicroseconds(1);
	digitalWrite(latchPin, LOW);
}

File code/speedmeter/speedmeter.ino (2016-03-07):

/*
 * This sketch can display an arbitrary ASCII string on the
 * Display. Right now it's used as a speedmeter to display
 * the rotational frequency.
 * Please note that the first 32 characters are not available,
 * and that the pipe character '|' (ASCII 124) is abused to
 * display 'µ'.
 */

#include <SPI.h>

// Look-up table with bitmap representations of ASCII chars

// 1st index: Character (ascii[i] = ASCII character i+32)
// 2nd index: row
// 3rd index: column
const byte ascii[][5][6] =
{
	// 32: space
	{
		{0b00000000, 0b00000000, 0b00000000, 0b00000000, 0b00000000, 0b00000000},
		{0b00000000, 0b00000000, 0b00000000, 0b00000000, 0b00000000, 0b00000000},
		{0b00000000, 0b00000000, 0b00000000, 0b00000000, 0b00000000, 0b00000000},
		{0b00000000, 0b00000000, 0b00000000, 0b00000000, 0b00000000, 0b00000000},
		{0b00000000, 0b00000000, 0b00000000, 0b00000000, 0b00000000, 0b00000000}
	},

	// 33: !
	{
		{0b00000000, 0b00000000, 0b00000000, 0b00000000, 0b00000000, 0b00000000},
		{0b00000000, 0b00000000, 0b00000000, 0b00000000, 0b00000000, 0b00000000},
		{0b00000000, 0b00000000, 0b00000000, 0b00001001, 0b00100100, 0b10000010},
		{0b00000000, 0b00000000, 0b00000000, 0b00000000, 0b00000000, 0b00000000},
		{0b00000000, 0b00000000, 0b00000000, 0b00000000, 0b00000000, 0b00000000}
	},

	// 34: "
	{
		{0b00000000, 0b00000000, 0b00000000, 0b00000000, 0b00000000, 0b00000000},
		{0b00000000, 0b00000000, 0b00000000, 0b00001001, 0b00000000, 0b00000000},
		{0b00000000, 0b00000000, 0b00000000, 0b00000000, 0b00000000, 0b00000000},
		{0b00000000, 0b00000000, 0b00000000, 0b00001001, 0b00000000, 0b00000000},
		{0b00000000, 0b00000000, 0b00000000, 0b00000000, 0b00000000, 0b00000000}
	},

	// 35: #
	{
		{0b00000000, 0b00000000, 0b00000000, 0b00000000, 0b00100000, 0b10000000},
		{0b00000000, 0b00000000, 0b00000000, 0b00000001, 0b00100100, 0b10010000},
		{0b00000000, 0b00000000, 0b00000000, 0b00000000, 0b00100000, 0b10000000},
		{0b00000000, 0b00000000, 0b00000000, 0b00000001, 0b00100100, 0b10010000},
		{0b00000000, 0b00000000, 0b00000000, 0b00000000, 0b00100000, 0b10000000}
	},

	// 36: $
	{
		{0b00000000, 0b00000000, 0b00000000, 0b00000001, 0b00000000, 0b10000000},
		{0b00000000, 0b00000000, 0b00000000, 0b00000001, 0b00000100, 0b00010000},
		{0b00000000, 0b00000000, 0b00000000, 0b00001001, 0b00100100, 0b10010010},
		{0b00000000, 0b00000000, 0b00000000, 0b00000001, 0b00000100, 0b00010000},
		{0b00000000, 0b00000000, 0b00000000, 0b00000000, 0b00100000, 0b00010000}
	},

	// 37: %
	{
		{0b00000000, 0b00000000, 0b00000000, 0b00000001, 0b00000000, 0b00010010},
		{0b00000000, 0b00000000, 0b00000000, 0b00000000, 0b00100000, 0b00010010},
		{0b00000000, 0b00000000, 0b00000000, 0b00000000, 0b00000100, 0b00000000},
		{0b00000000, 0b00000000, 0b00000000, 0b00001001, 0b00000000, 0b10000000},
		{0b00000000, 0b00000000, 0b00000000, 0b00001001, 0b00000000, 0b00010000}
	},

	// 38: &
	{
		{0b00000000, 0b00000000, 0b00000000, 0b00000000, 0b00000000, 0b10000010},
		{0b00000000, 0b00000000, 0b00000000, 0b00000000, 0b00000000, 0b00010000},
		{0b00000000, 0b00000000, 0b00000000, 0b00000001, 0b00100000, 0b10000010},
		{0b00000000, 0b00000000, 0b00000000, 0b00001000, 0b00000100, 0b00000010},
		{0b00000000, 0b00000000, 0b00000000, 0b00000001, 0b00100000, 0b10010000}
	},

	// 39: '
	{
		{0b00000000, 0b00000000, 0b00000000, 0b00000000, 0b00000000, 0b00000000},
		{0b00000000, 0b00000000, 0b00000000, 0b00000000, 0b00000000, 0b00000000},
		{0b00000000, 0b00000000, 0b00000000, 0b00001001, 0b00000000, 0b00000000},
		{0b00000000, 0b00000000, 0b00000000, 0b00000000, 0b00000000, 0b00000000},
		{0b00000000, 0b00000000, 0b00000000, 0b00000000, 0b00000000, 0b00000000}
	},

	// 40: (
	{
		{0b00000000, 0b00000000, 0b00000000, 0b00001000, 0b00000000, 0b00000010},
		{0b00000000, 0b00000000, 0b00000000, 0b00000001, 0b00000000, 0b00010000},
		{0b00000000, 0b00000000, 0b00000000, 0b00000000, 0b00100100, 0b10000000},
		{0b00000000, 0b00000000, 0b00000000, 0b00000000, 0b00000000, 0b00000000},
		{0b00000000, 0b00000000, 0b00000000, 0b00000000, 0b00000000, 0b00000000}
	},

	// 41: )
	{
		{0b00000000, 0b00000000, 0b00000000, 0b00000000, 0b00000000, 0b00000000},
		{0b00000000, 0b00000000, 0b00000000, 0b00000000, 0b00000000, 0b00000000},
		{0b00000000, 0b00000000, 0b00000000, 0b00000000, 0b00100100, 0b10000000},
		{0b00000000, 0b00000000, 0b00000000, 0b00000001, 0b00000000, 0b00010000},
		{0b00000000, 0b00000000, 0b00000000, 0b00001000, 0b00000000, 0b00000010}
	},

	// 42: *
	{
		{0b00000000, 0b00000000, 0b00000000, 0b00000000, 0b00100000, 0b10000000},
		{0b00000000, 0b00000000, 0b00000000, 0b00000000, 0b00000100, 0b00000000},
		{0b00000000, 0b00000000, 0b00000000, 0b00000001, 0b00100100, 0b10010000},
		{0b00000000, 0b00000000, 0b00000000, 0b00000000, 0b00000100, 0b00000000},
		{0b00000000, 0b00000000, 0b00000000, 0b00000000, 0b00100000, 0b10000000}
	},

	// 43: +
	{
		{0b00000000, 0b00000000, 0b00000000, 0b00000000, 0b00000100, 0b00000000},
		{0b00000000, 0b00000000, 0b00000000, 0b00000000, 0b00000100, 0b00000000},
		{0b00000000, 0b00000000, 0b00000000, 0b00000001, 0b00100100, 0b10010000},
		{0b00000000, 0b00000000, 0b00000000, 0b00000000, 0b00000100, 0b00000000},
		{0b00000000, 0b00000000, 0b00000000, 0b00000000, 0b00000100, 0b00000000}
	},

	// 44: ,
	{
		{0b00000000, 0b00000000, 0b00000000, 0b00000000, 0b00000000, 0b00000000},
		{0b00000000, 0b00000000, 0b00000000, 0b00000000, 0b00000000, 0b00000000},
		{0b00000000, 0b00000000, 0b00000000, 0b00000000, 0b00000000, 0b00000000},
		{0b00000000, 0b00000000, 0b00000000, 0b00000000, 0b00000100, 0b10010000},
		{0b00000000, 0b00000000, 0b00000000, 0b00000000, 0b00000100, 0b10000010}
	},

	// 45: -
	{
		{0b00000000, 0b00000000, 0b00000000, 0b00000000, 0b00000100, 0b00000000},
		{0b00000000, 0b00000000, 0b00000000, 0b00000000, 0b00000100, 0b00000000},
		{0b00000000, 0b00000000, 0b00000000, 0b00000000, 0b00000100, 0b00000000},
		{0b00000000, 0b00000000, 0b00000000, 0b00000000, 0b00000100, 0b00000000},
		{0b00000000, 0b00000000, 0b00000000, 0b00000000, 0b00000100, 0b00000000}
	},

	// 46: .
	{
		{0b00000000, 0b00000000, 0b00000000, 0b00000000, 0b00000000, 0b00000000},
		{0b00000000, 0b00000000, 0b00000000, 0b00000000, 0b00000000, 0b00000000},
		{0b00000000, 0b00000000, 0b00000000, 0b00000000, 0b00000000, 0b00010010},
		{0b00000000, 0b00000000, 0b00000000, 0b00000000, 0b00000000, 0b00010010},
		{0b00000000, 0b00000000, 0b00000000, 0b00000000, 0b00000000, 0b00000000}
	},

	// 47: /
	{
		{0b00000000, 0b00000000, 0b00000000, 0b00000001, 0b00000000, 0b00000000},
		{0b00000000, 0b00000000, 0b00000000, 0b00000000, 0b00100000, 0b00000000},
		{0b00000000, 0b00000000, 0b00000000, 0b00000000, 0b00000100, 0b00000000},
		{0b00000000, 0b00000000, 0b00000000, 0b00000000, 0b00000000, 0b10000000},
		{0b00000000, 0b00000000, 0b00000000, 0b00000000, 0b00000000, 0b00010000}
	},
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

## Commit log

2014-12-16 First commit
    Arduino sketch that runs on a teensy 3.1 and updates the display’s LEDs
    via their SPI drivers. Rotation sync using a hall sensor.
2014-12-17 Added Animated in its own folder so that the Arduino IDE doesn't go crazy
2014-12-24 Added Eagle -sch and .brd files
    [3DPOV.brd, 3DPOV.sch]
2014-12-24 Renamed some files for clarity
    [Board.brd, Schematic.sch]
2014-12-29 Added floating average period meaurements for less jitter
    [_3DPOV.ino]
2015-01-31 Added program that displays current frequency and period
2015-03-07 correction about rightshift and division
    [_3DPOV.ino]
2016-03-07 Better folder structure
    [Board.brd, Schematic.sch]
2016-03-07 Moved sketches for arduino IDE

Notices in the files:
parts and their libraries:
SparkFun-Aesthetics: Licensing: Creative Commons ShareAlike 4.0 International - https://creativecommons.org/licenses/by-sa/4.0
